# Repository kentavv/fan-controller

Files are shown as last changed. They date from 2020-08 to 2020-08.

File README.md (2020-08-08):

# fan-controller
A temperature driven fan controller with a Nextion touchscreen display and Arduino reading contact and non-contact temperature sensors.

I use the fan controller to control a cooling fan of an AC servo motor used as a spindle motor on a CNC mill.

An overview of the project is available in [video form](https://www.youtube.com/watch?v=nkzJMKOuecU).

# Bill of materials

Below are links to the items that I used. Most of these are Amazon Affiliate links.

## Arduino
I prefer the Arduino Uno with a socketed DIP since it's easily repairable, but the SMD version is a little less expensive. The bare shield is a convenient for mounting all.

[Arduino Uno R3, DIP version](https://amzn.to/2Ekh8hU)

[Arduino Uno R3, SMD version](https://amzn.to/3jF4XfJ)

[Arduino Uno R3 Bare Shield](https://amzn.to/3hA0Lfq)

[Straight Headers](https://amzn.to/2ZXLKOt)

## Power conversion
A Murata DC-DC converter supplies 12V to the Arduino Uno from the 24V source that also powers the fan. (The Arduino Uno's regulator supplies the display and sensors.) To reduce height, the converter should be mounted flush with the shield. The W36H model is easiest to mount, but the W36 model can be mounted to a right-angle header.

[Murata DC-DC Converter OKI-78SR-12/1.0-W36H-C](https://www.digikey.com/product-detail/en/murata-power-solutions-inc/OKI-78SR-12-1-0-W36H-C/811-3294-ND/6817699)

or 

[Right-angle Headers](https://amzn.to/39v0EPC)

[Murata DC-DC Converter OKI-78SR-12/1.0-W36-C](https://www.digikey.com/product-detail/en/murata-power-solutions-inc/OKI-78SR-12-1-0-W36-C/811-3293-ND/6817698)

## Display
The GPIO board is not required, but will useful if you wish to use the Nextion display for other projects. The display can generate a PWM signal, which might control the fan. But, reading the fan tach or the temperature sensors may not be possible with the display.

[Nextion Enhanced NX4832K035](https://amzn.to/2BzLn3o)

[Nextion GPIO Breakout](https://amzn.to/300HcXz)

## Temperature sensor
The DS18B20 and OTI-301 were used. The OTI-301 has a response curve in its manual, but the MLX90614ESF has a richer datasheet. The OTI-301 is also harder to find than the MLX90614ESF.

[DS18B20-based Contact Temperature Sensor](https://amzn.to/32WuU4u)

[OTI-301-based Non-contact Temperature Sensor](https://amzn.to/32WzyzE)

[MLX90614ESF-based Non-contact Temperature Sensor](https://amzn.to/2CQswS5)

## Fan
I used a 24V fan because there was an existing 24V supply. Could use a 12V computer fan instead. The Noctua fans come with pain extensions or extensions with built-in resistors. Either can be modified to serve as a pigtail from the Arduino to the fan.

[Noctua NF-F12 industrialPPC-24V-3000 Q100 IP67 PWM](https://amzn.to/3g4mzQ6)

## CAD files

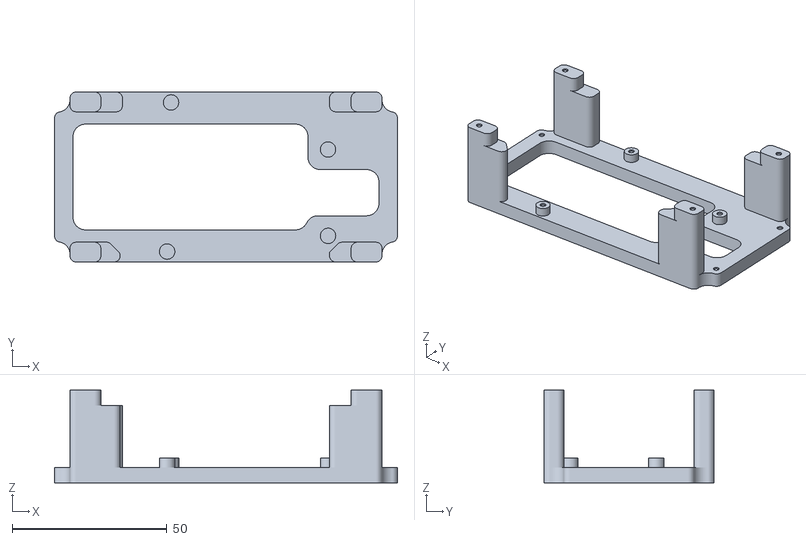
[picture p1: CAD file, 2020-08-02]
holder.stl
111.0 x 55.0 x 30.0

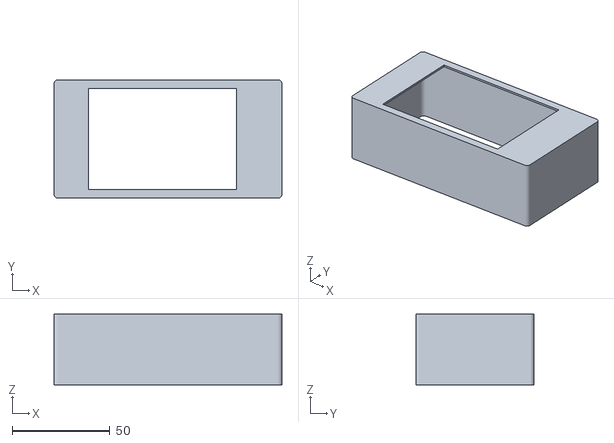
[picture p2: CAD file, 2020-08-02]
surround.stl
116.5 x 60.5 x 36.2

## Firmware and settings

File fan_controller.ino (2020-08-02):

// Arduino Uno pintout: https://upload.wikimedia.org/wikipedia/commons/c/c9/Pinout_of_ARDUINO_Board_and_ATMega328PU.svg
// Arduino Uno PWM is 490Hz on all PWM pins except pins 5 & 6 which have 980Hz PWM: https://www.arduino.cc/reference/en/language/functions/analog-io/analogwrite/
//
// To communicate with the display, AltSoftSerial is used, retaining use of the Arduino's USB serial.
// AltSoftSerial docs: https://www.pjrc.com/teensy/td_libs_AltSoftSerial.html
// AltSoftSerial disables PWM on Ardunio Uno pin 10, transmits on pin 9 and receives on pin 8
//
// Tested with: Nextion Enhanced 3.5" HMI Resistive Touch Screen UART LCD Display Module NX4832K035 480x320
// https://nextion.tech/datasheets/nx4832k035/
// Nextion display instruction set: https://nextion.tech/instruction-set/
// Nice Nextion tutorial: https://www.seithan.com/projects/nextion-tutorial/

#define INCLUDE_CS 0
#define INCLUDE_NCS 1

#if INCLUDE_CS
#include <DallasTemperature.h>
#include <OneWire.h>
#endif

#if INCLUDE_NCS
#include <Wire.h>
#endif

#include <AltSoftSerial.h>

const struct {
  int h = 220; // the height of the Nextion graph
  float min_temp = 24; // the minimum temperature shown on graph
  float max_temp = 100; // the maximum temperature shown on the graph
  float max_fan_rpm = 3000.; // the maximum fan speed shown on the graph
} graph_config;
      
const struct {
  // The minimum temperature at which fan will run and the PWM value
  float min_temp = 29.;
  int min_pwm = 50;

  // The minimum temperature at which fan will run at full speed
  float max_temp = 34.;
  int max_pwm = 255;

  float deadzone = .2; // hysteresis band: +/- deadzone
} fan_config;

#if INCLUDE_CS
const int one_wire_pin = 4;
#endif

const int pwm_pin = 5;
const int tach_pin = 3;

bool nextion_debug = false;

volatile int fan_pulse_count = 0;
int last_fan_rpm = 0;
unsigned long last_fan_start = 0;
int last_fan_pwm = 0;

enum {TEMP_C, TEMP_F} temp_mode = TEMP_C;
enum {FAN_MIN, FAN_AUTO, FAN_MAX} fan_mode = FAN_AUTO;

const unsigned long fan_tach_sample_dt = 1000;
const int fan_ppr = 2; // two pulses per fan revolution
const int display_update_dt = 500;
const int fan_mode_update_dt = 2000;
const int graph_update_dt = 5000;

unsigned long last_display_read = 0;
unsigned long last_display_update = 0;
unsigned long last_graph_update = 0;
unsigned long last_fan_mode_change = 0;
unsigned long last_temp_mode_change = 0;
char nex_buffer[128]; // temp variable holding Nextion command string

AltSoftSerial altSerial; // Pins tx:9 rc:8, Nextion: yellow->9, blue->8
#if INCLUDE_CS
OneWire oneWire(one_wire_pin);
DallasTemperature sensors(&oneWire);
#endif

void isr_fan_pulse();
void find_min_max();
void send_to_nextion(char ss[]);

void setup(void) {
  pinMode(pwm_pin, OUTPUT);
  pinMode(tach_pin, INPUT_PULLUP);

  Serial.begin(9600);
  altSerial.begin(38400);

#if INCLUDE_CS
  sensors.begin();
  sensors.setResolution(9);
  // Serial.print("Parasitic power needed:");
  // Serial.println(sensors.isParasitePowerMode());
#endif

#if INCLUDE_NCS
  Wire.begin();
#endif

  last_fan_start = millis();
  attachInterrupt(digitalPinToInterrupt(tach_pin), isr_fan_pulse, RISING);

  //  find_min_max();

  if (nextion_debug) {
    // Nextion default is to only send a response to a command if there's an error
    send_to_nextion("bkcmd=3");
  }

  send_to_nextion("page 0");
}

void isr_fan_pulse () {
  // Count each fan tach pulse in this interrupt handler
  fan_pulse_count++;
}

int reset_fan_counts() {
  int rv;

  cli();
  rv = fan_pulse_count;
  fan_pulse_count = 0;
  last_fan_start = millis();
  sei();

  return rv;
}

int fan_speed(bool force_update = false) {
  unsigned long cur = millis();

  unsigned long dt = cur - last_fan_start;

  if (force_update && dt < fan_tach_sample_dt) {
    delay(fan_tach_sample_dt - dt + 1);
    cur = millis();
    dt = cur - last_fan_start;
  }

  if (dt > fan_tach_sample_dt) {
    int cnt = reset_fan_counts();

    // Avoid overflow with careful order of operations
    last_fan_rpm = cnt * (60UL * 1000) / (dt * fan_ppr);
  }

  return last_fan_rpm;
}

void set_fan_speed(int fan_pwm) {
  analogWrite(pwm_pin, fan_pwm);
  last_fan_pwm = fan_pwm;
}

//void find_min_max() {
//  for (int fan_pwm = 0; fan_pwm < 256; fan_pwm += 5) {
//    set_fan_speed(fan_pwm);
//
//    delay(500); // Give the fan time to stabilize
//
//    reset_fan_counts();
//
//    int rpm = fan_speed(true); // Block until RPM is read
//
//    Serial.print(fan_pwm);
//    Serial.print(" ");
//    Serial.println(rpm);
//  }
//}

int target_fan_pwm(float temp) {
  int rv = 0;

  switch (fan_mode) {
    case FAN_MIN: rv = fan_config.min_pwm; break;
    case FAN_MAX: rv = fan_config.max_pwm; break;
    case FAN_AUTO:
    default:
      if (temp < fan_config.min_temp) {
        rv = 0;
      } else {
        int tmp = (temp - fan_config.min_temp) / (fan_config.max_temp - fan_config.min_temp) * fan_config.max_pwm;
        rv = min(max(tmp, fan_config.min_pwm), fan_config.max_pwm);
      }
      if (rv != last_fan_pwm) {
        if (fabs(temp - fan_config.min_temp) < fan_config.deadzone || fabs(temp - fan_config.max_temp) < fan_config.deadzone) {
          rv = last_fan_pwm;
        }
      }
      break;
  }

  last_fan_pwm = rv;

  return rv;
}

bool nextion_check_return() {
  bool rv = true;

  delay(10); // small delay so that the last command can complete. What is the
  // longest that a command might take to complete?

  // TODO: Needed improvements to make this code more robust:
  //   1) look for the trailing flag 0xff 0xff 0xff;
  //   2) timeout if the trailing flag is not received within a timeout period;
  //   3) reset the response buffer index (i) after parsing a command.

  const int n_buf = 8;
  unsigned char response[n_buf];
  if (altSerial.available()) {
    int i;
    for (i = 0; i < n_buf && altSerial.available(); i++) {
      unsigned char c = altSerial.read();
      response[i] = c;
      if (nextion_debug) {
        Serial.print("0x");
        Serial.print((int)c, HEX);
        Serial.print(" ");
      }
    }
    if (nextion_debug) {
      Serial.print("\n");
    }

    if (i == 6 && response[0] == 0x00 && response[1] == 0x00 && response[2] == 0x00) {
      //  Nextion Startup
    } else if (i > 2 && response[0] == 0x24) { // Serial Buffer Overflow
    } else if (i > 2 && response[0] == 0x65) { // Touch Event
      unsigned char page_num = response[1];
      unsigned char comp_id = response[2];
      unsigned char event = response[3];

      if (page_num == 0x00 && event == 0x00) {
        if (comp_id == 0x09) {
          temp_mode = (temp_mode + 1) % 2;
          if (nextion_debug) {
            Serial.println("Change temp_mode");
          }
          last_temp_mode_change = millis();
        } else if (comp_id == 0x0a) {
          fan_mode = (fan_mode + 1) % 3;
          if (nextion_debug) {
            Serial.println("Change fan_mode");
          }
          last_fan_mode_change = millis();
        }
      }
    } else if (i > 2 && response[0] == 0x66) { // Current Page Number
    } else if (i > 2 && response[0] == 0x67) { // Touch Coordinate (awake)
    } else if (i > 2 && response[0] == 0x68) { // Touch Coordinate (sleep)
    } else if (i > 2 && response[0] == 0x70) { // String Data Enclosed
    } else if (i > 2 && response[0] == 0x71) { // Numeric Data Enclosed
    } else if (i > 2 && response[0] == 0x86) { // Auto Entered Sleep Mode
    } else if (i > 2 && response[0] == 0x87) { // Auto Wake from Sleep
    } else if (i > 2 && response[0] == 0x88) { // Nextion Ready
    } else if (i > 2 && response[0] == 0x89) { // Start microSD Upgrade
    } else if (i > 2 && response[0] == 0xfd) { // Transparent Data Finished
    } else if (i > 2 && response[0] == 0xfe) { // Transparent Data Ready
    } else if (i > 2 && 0 <= response[0] && response[0] <= 0x23) {
      switch (response[0]) {
        case 0x01: // Instruction Successful
          rv = true;
          break;
        case 0x00: // Invalid Instruction
        case 0x02: // Invalid Component ID
        case 0x03: // Invalid Page ID
        case 0x04: // Invalid Picture ID
        case 0x05: // Invalid Font ID
        case 0x06: // Invalid File Operation
        case 0x09: // Invalid CRC
        case 0x11: // Invalid Baud rate Setting
        case 0x12: // Invalid Waveform ID or Channel #
        case 0x1a: // Invalid Variable name or attribute
        case 0x1b: // Invalid Variable Operation
        case 0x1c: // Assignment failed to assign
        case 0x1d: // EEPROM Operation failed
        case 0x1e: // Invalid Quantity of Parameters
        case 0x1f: // IO Operation failed
        case 0x20: // Escape Character Invalid
        case 0x23: // Variable name too long
          rv = false;
          break;
        default:
          Serial.print("Unknown Nextion error code: ");
          Serial.println(response[0], HEX);
          break;
      }
    } else {
      Serial.print("Unknown Nextion code: ");
      for (int j = 0; j < i; j++) {
        unsigned char c = response[j];
        Serial.print("0x");
        Serial.print((int)c, HEX);
        Serial.print(" ");
      }
      Serial.print("\n");
    }
  }

  return rv;
}

void send_to_nextion(char ss[]) {
  if (nextion_debug) {
    Serial.println(ss);
  }

  altSerial.print(ss);
  altSerial.write(0xff);
  altSerial.write(0xff);
  altSerial.write(0xff);

  if (! nextion_check_return()) {
    Serial.print("Potentially failed command: ");
    Serial.println(ss);
  }
}

//void debug_rtc() {
//  const int n = 6;
//  const char *vars[n] = {"rtc2", "rtc3", "rtc4", "rtc5", "sys2", "va1.val"};
//
//  for (int i = 0; i < n; i++) {
//    sprintf(nex_buffer, "covx %s,va4.txt,0,0\xff\xff\xffxstr 0,%d,150,40,0,65000,0,2,1,1,va4.txt", vars[i], i * 40);
//    send_to_nextion(nex_buffer);
//  }
//}

void update_display(float temp, int fan_rpm) {
  unsigned long cur = millis();
  bool updated = false;

  if (cur - last_display_update > display_update_dt) {
    // debug_rtc();

    last_display_update = cur;
    updated = true;

    {
      char unit = 'C';
      float v = temp;

      if (temp_mode == TEMP_F) {
        v = temp * (9. / 5.) + 32.;
        unit = 'F';
      }

      char fstr[6];
      dtostrf(v, 0, 1, fstr);
      sprintf(nex_buffer, "b0.txt=\"%s %c\"", fstr, unit);
      send_to_nextion(nex_buffer);
    }

    {
      if (cur - last_fan_mode_change < fan_mode_update_dt) {
        switch (fan_mode) {
          case FAN_MIN: sprintf(nex_buffer, "b1.txt=\"Min RPM\""); break;
          case FAN_MAX: sprintf(nex_buffer, "b1.txt=\"Max RPM\""); break;
          case FAN_AUTO:
          default: sprintf(nex_buffer, "b1.txt=\"Auto RPM\""); break;
        }
      } else {
        switch (fan_mode) {
          case FAN_MIN: sprintf(nex_buffer, "b1.txt=\"%d mRPM\"", fan_rpm); break;
          case FAN_MAX: sprintf(nex_buffer, "b1.txt=\"%d MRPM\"", fan_rpm); break;
          case FAN_AUTO:
          default: sprintf(nex_buffer, "b1.txt=\"%d RPM\"", fan_rpm); break;
        }

      }
      send_to_nextion(nex_buffer);
    }
  }

  if (cur - last_graph_update > graph_update_dt) {
    last_graph_update = cur;
    updated = true;

    {
      int v = (int)((temp - graph_config.min_temp) / (graph_config.max_temp - graph_config.min_temp) * graph_config.h);
      v = min(max(0, v), graph_config.h);
      sprintf(nex_buffer, "add 1,0,%d", v);
      send_to_nextion(nex_buffer);
    }

    {
      int v = (int)(fan_rpm / graph_config.max_fan_rpm * graph_config.h);
      v = min(max(0, v), graph_config.h);
      sprintf(nex_buffer, "add 1,1,%d", v);
      send_to_nextion(nex_buffer);
    }
  }

  if (! updated) {
    nextion_check_return();
  }
}

#if INCLUDE_NCS
bool read_nc_temp(float &tmp) {
  bool rv = false;
  const int addr = 0x10; // I2C addresses at 7-bit, must shift documented 0x20 address, so 0x10.

  Wire.beginTransmission(addr);
  Wire.write(0x80);
  int rv2 = Wire.endTransmission(false);

  if (rv2 != 0) {
    Serial.print("Error while transmitting: ");
    Serial.println(rv2);
  } else {
    const int n = 6;
    uint8_t dat[n];

    Wire.requestFrom(addr, n);

    int i;
    for (i = 0; i < n && Wire.available(); i++) {
      dat[i] = Wire.read();
    }

    if (i != n) {
      Serial.println("Incomplete data");
    } else {
      float amb = (dat[2] * 65536L + dat[1] * 256L + dat[0]) / 200.;
      float obj = (dat[5] * 65536L + dat[4] * 256L + dat[3]) / 200.;

//      Serial.print("Temperatures (C): Ambient: ");
//      Serial.print(amb);
//      Serial.print("  Object: ");
//      Serial.println(obj);

      tmp = obj;
      rv = true;
    }
  }

  return rv;
}
#endif

void loop(void) {
  float temp=0, nc_temp=0;

#if INCLUDE_CS
  // The combintion of request and retrieval is a slow operation. At 12-bit
  // resolution ~540ms and at 9-bit resolution ~120ms.
  // Can make a non-blocking request by calling sensors.setWaitForConversion(false)
  // before sensors.requestTemperatures(). This requires polling to check if conversion
  // is complete. See DallasTemperature::blockTillConversionComplete() for details.
  sensors.requestTemperatures();
  temp = sensors.getTempCByIndex(0);
#endif

  // Compared to the contact temperature sensor, the non-contact sensor is 
  // essentially instant.
#if INCLUDE_NCS
  if (read_nc_temp(nc_temp)) {
    Serial.print("Contact:");
    Serial.print(temp);
    Serial.print(" Non-contact:");
    Serial.println(nc_temp);

    temp = nc_temp;
  }
#endif

  int new_fan_pwm = target_fan_pwm(temp);
  set_fan_speed(new_fan_pwm);
  int fan_rpm = fan_speed();

  update_display(temp, fan_rpm);
}

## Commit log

2020-07-31 Optionally compile in contact and non-contact sensor support
2020-08-02 Added model files
    [holder.stl, surround.stl]
